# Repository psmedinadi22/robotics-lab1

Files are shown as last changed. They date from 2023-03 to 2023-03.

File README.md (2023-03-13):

# robotics-lab1
Repositoty for practices with an industrial robot model ABB IRB140

> ## Contributors
> 
> - [Camilo Andrés Borda Gil](https://github.com/Canborda) (caabordagi@unal.edu.co)
> - Paula Sofía Medina Diaz (psmedinadi@unal.edu.co)
> - Robinson Jair Orduxz Gomez (rjorduzg@unal.edu.co)

---
# Tool Design

The goal was to draw on a defined surface with a self-designed tool. To achieve this, we searched on the [product manual](https://library.e.abb.com/public/81a35b138c2342b5b9455e5696a09484/3HAC027400%20PM%20IRB%20140-en.pdf) the dimensions of the mounting flange.

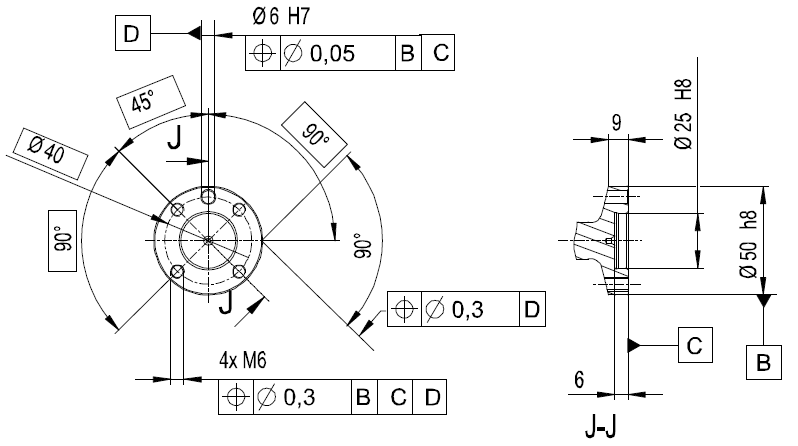
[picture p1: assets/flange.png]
holes on mounting flange


Based on those dimensions, the team designed the tool shown below, made up of four parts: a base and a cap build with 3D printing, a spring and a marker. To see the tool model with more detail go to <a target="_blank" href="https://cad.onshape.com/documents/02a2a5fe444c220951f7859a/w/4de4b01172907f48fb48adbe/e/481b6444fafd2e1357d20adc">Visualize CAD model with OnShape</a>.

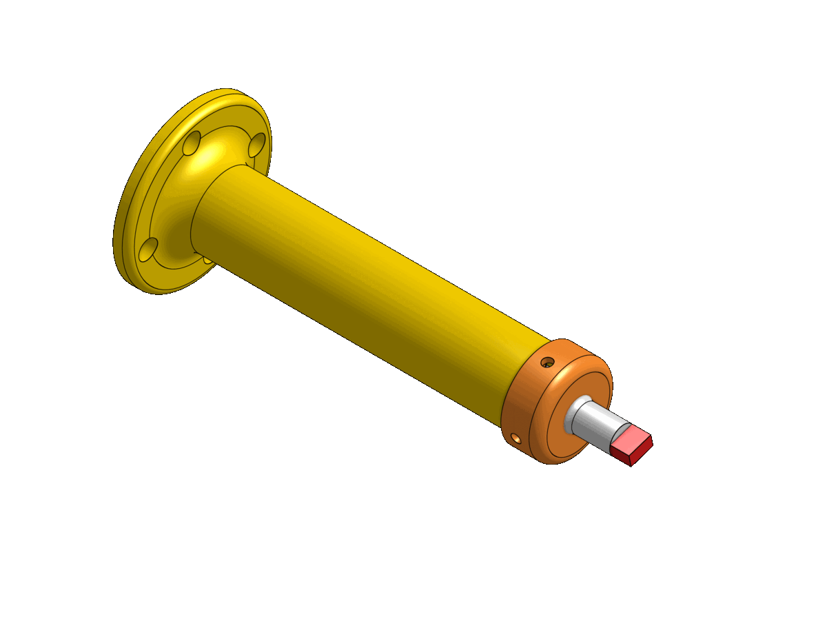
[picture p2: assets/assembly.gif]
tool assembly


The final tool has the following properties:
| | |
|---|---|
| __mass__ | $34g$ (parts) + $70g$ (marker) |
| __center of gravity__ | $[0, 0, 61]$ $\text{mm}$ |
| __TCP__ | $[0, 0, 145]$ $\text{mm}$ |

---
# Tool Calibration

The calibration process starts by fixing the tool on the mounting flange with four screws. Next, using the jogging function and the joystick, the TCP (Tool Center Point) must be matched with an external pointed tool in four different configurations of the robot. Once all four positions have been achieved the robot controller will calculate with inverse kinematics the TCP frame offset with respect to the `tool0` frame. The program also shows the error found in the calculation.

> - __Position__: $\{ x=-1.14511, y=-2.77919, z=147.51\}$
> - __Error__: $\{max=1.1265782\text{ mm}, min=0.3530322\text{ mm}, mean=0.6549213\text{ mm}\}$

---
# Simulation
Before any application on an industrial robot, it's mandatory to simulate the process to ensure that all paths the robot will make are safe. For this simulation stage we use [RobotStudio®](https://new.abb.com/products/robotics/robotstudio) software, following these steps:

1. Create a new station and add the robot model [ABB - IRB140](https://new.abb.com/products/3HAC020536-001/irb-140), the created tool (modeled in the _Tool Design_ section) and the work object with the surface to write to. Both tool and object models are imported in `.sat` format (available at [/models](./models) folder).
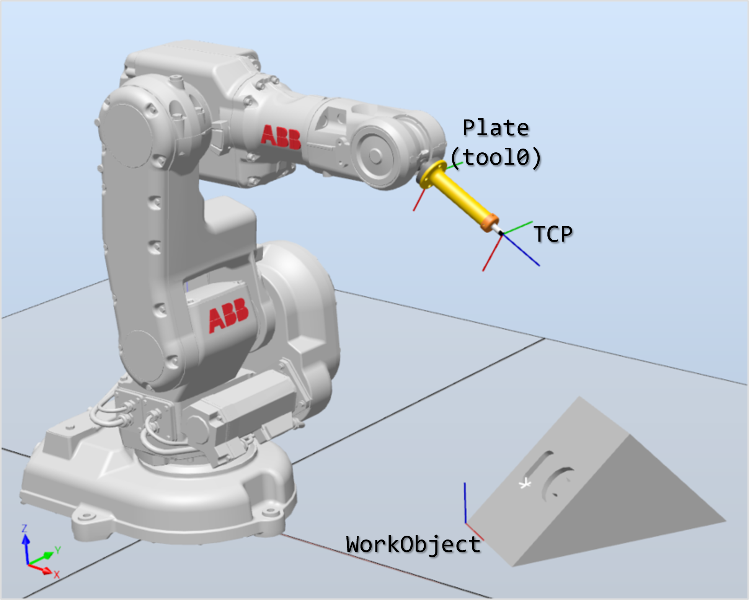
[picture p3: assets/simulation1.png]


2. Configure <b>TCP</b> (Tool Center Point) by adding the position and orientation offset with respect to the `tool0` frame. This offset can be obtained from the tool model or via tool calibration as described in the previous section.
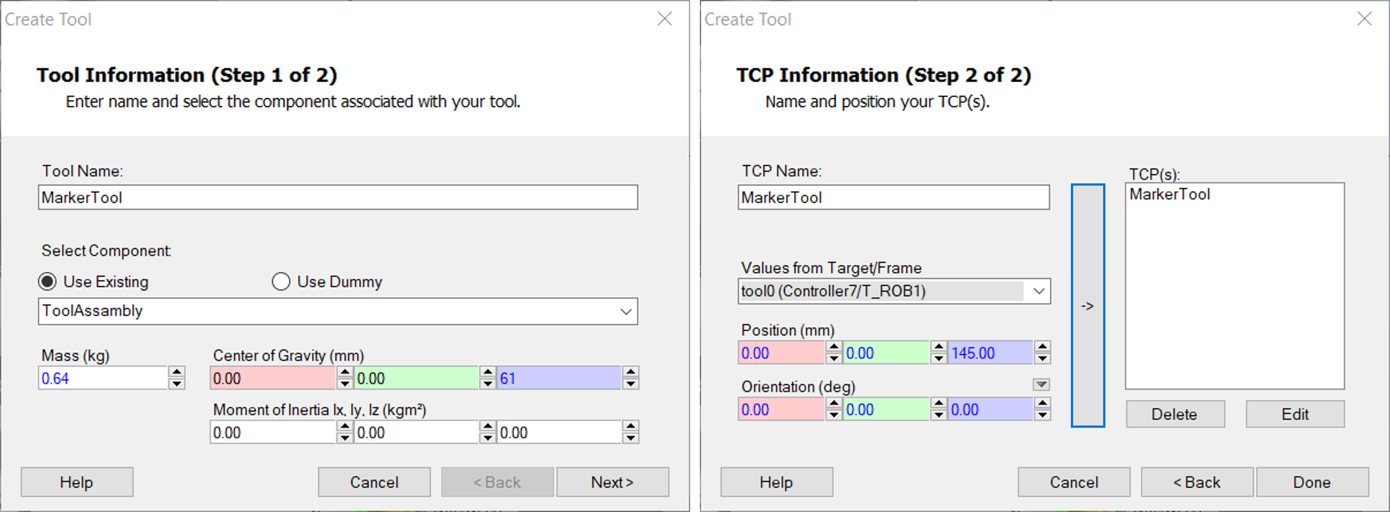
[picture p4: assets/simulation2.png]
tool creation configuration


3. Generate path with the `AutoPath` tool. It is possible to set the tolerance, the speed and the correction for reduced angles.
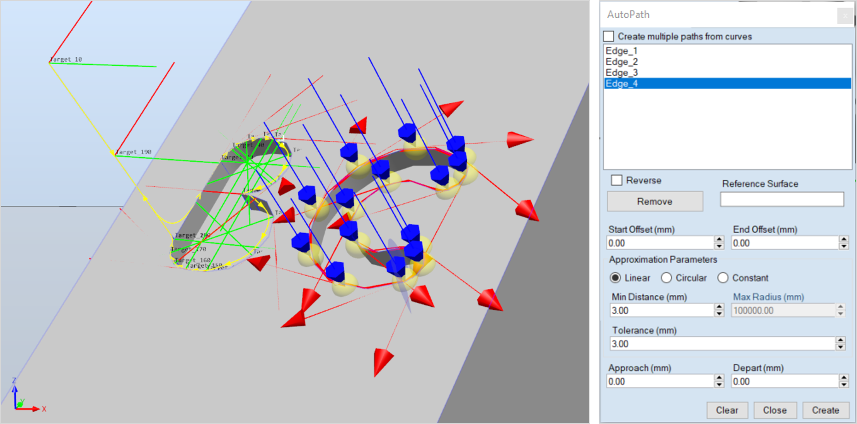
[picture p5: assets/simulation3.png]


4. Create midway points to ensure a safe trajectory for the robot as it approaches to the designed path.
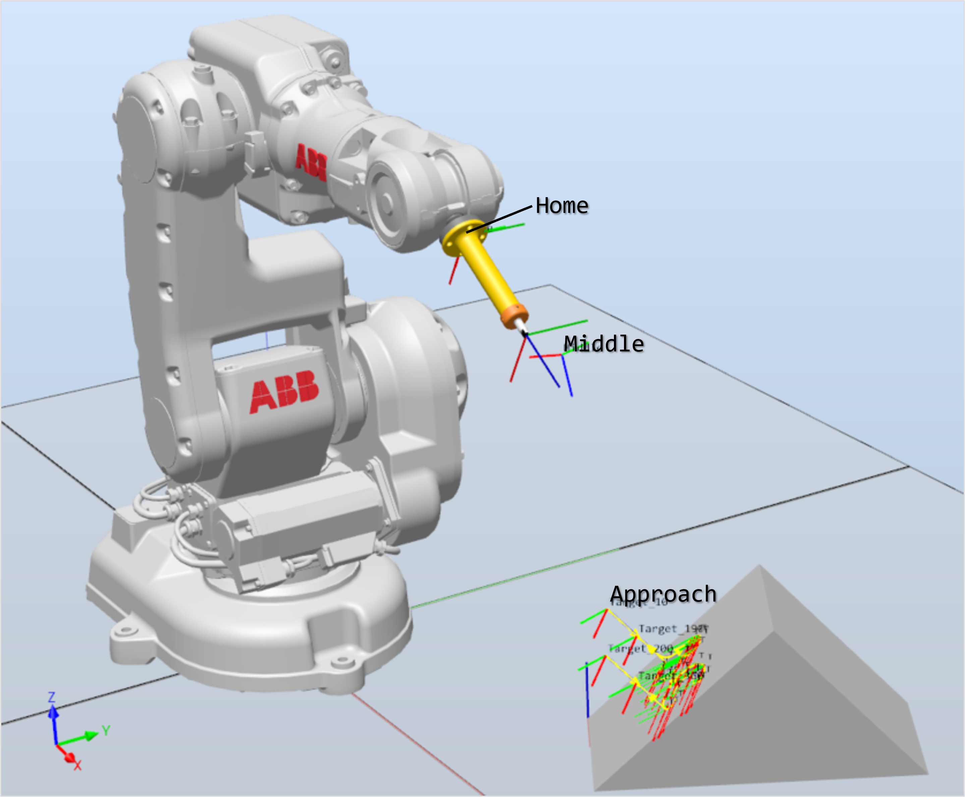
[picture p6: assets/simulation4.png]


5. Create subroutine on RAPID code by calling the different PROCEDURES into the `main()` function. RobotStudio will create the constants for every targed used in the different paths and will also write every path as an isolated procedure. The final RAPID code is available inside the [/code](./code/Module1.mod) folder.
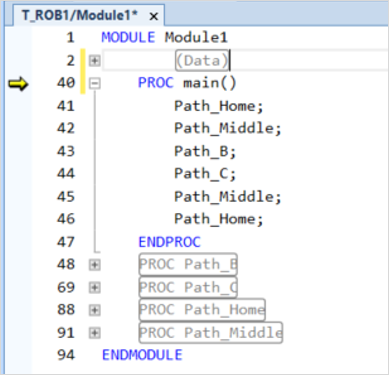
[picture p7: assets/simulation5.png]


https://user-images.githubusercontent.com/55401093/188253709-890514b5-370a-47eb-8e7b-e0c88d74943e.mp4

---
# Demonstration

https://user-images.githubusercontent.com/55401093/188254255-55779791-179b-4d6a-8675-2d9d4596900a.mp4

https://user-images.githubusercontent.com/55401093/188256259-78a9372b-4661-4763-ac9e-4cb798e6ed9c.mp4

---
# Conclusions

- Performing a simulation before the real robot implementation allows to solve problems and prevents dangerous situations for both robot and humans. It also helps to study the paths and obtain more complex and more accurate results by simplifying the path planning task and helping with all math inside.
- In the tool design it is important to acknowledge the requirements and limitations of the robot and thus avoid any damage. A tool must only be used in the task it was designed for.
- The precision on the calibration depends mostly on how well defined is the origin of the TCP, in this case, the wide shape of the marker tip made very difficult to find the exact point and that led to a bigger calibration error.
- About the work object calibration, the selection of the calibration points is very important because this will define how hard will be for the robot to follow the path using simple poses and sometimes a point can't be reached by the TCP.

---

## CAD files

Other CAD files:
models/Marker.ipt
models/Tool.ipt
models/ToolAssambly.iam
models/ToolCap.ipt
models/Triangle.ipt
